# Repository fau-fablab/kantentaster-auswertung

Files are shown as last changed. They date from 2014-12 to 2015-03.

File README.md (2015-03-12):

kantentaster-auswertung
=======================

##motivation
Initially CNC mills do not "know" where the material is.
If you want to mill through the material, you have to know exactly where your material is relatively to the machine coordinate system.

For this the typical tool is a 3D probe.
However this probe cannot simply be connected to the controller of the mill.
This project is a Schmitt-triggered current loop to adapt the probe to the controller.

##circuit
The typical design for such a 3D probe (in our case a Renishaw) is that you have a contact which opens upon touching something with the tip of the probe.
When not touching anything the resistance of the probe is in the range of 20k.
When touching something the resistance becomes very large.

To have a robust measurement this circuit uses a current loop.
It consists of a constant-current-source which constantly puts a current of 1mA through the sensor.
Attached to this circuit is a Schmitt-trigger.
The hysteresis levels are configurable, because the trigger has to be fine tuned "in field".

Finally the output is separated from the controller with an optocoupler, because the sensor cable runs through a potentially rough environment.

----------------------
##version history
The first version of the PCB is in directory ```kantentaster_platine```. This version did not work. A complete redesign and current development version is in ```kantentaster_v2```.

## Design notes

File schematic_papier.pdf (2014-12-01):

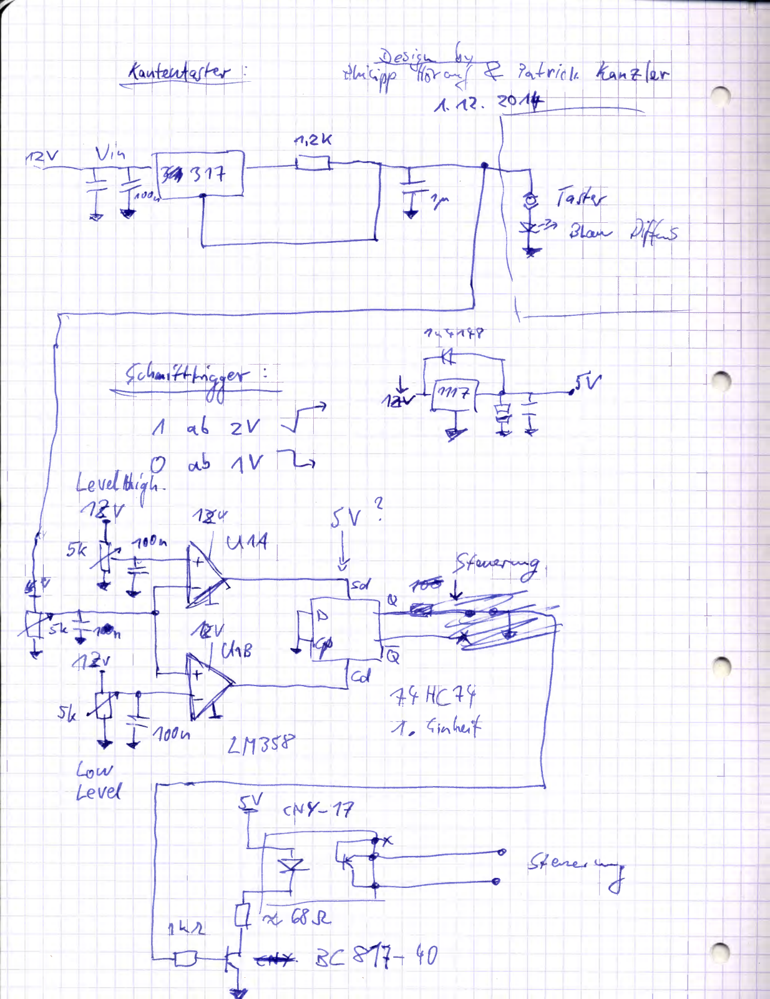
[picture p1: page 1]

-,1 ,.:c,~ T.,, -1-rirf, 4:.A„ ~ (o,.,..

A- '17. <~ L- --;-.

t

} 1
r

\/ cN Y- 11

.___--
~ '8JL
erO'- ?.C 1- Y 0

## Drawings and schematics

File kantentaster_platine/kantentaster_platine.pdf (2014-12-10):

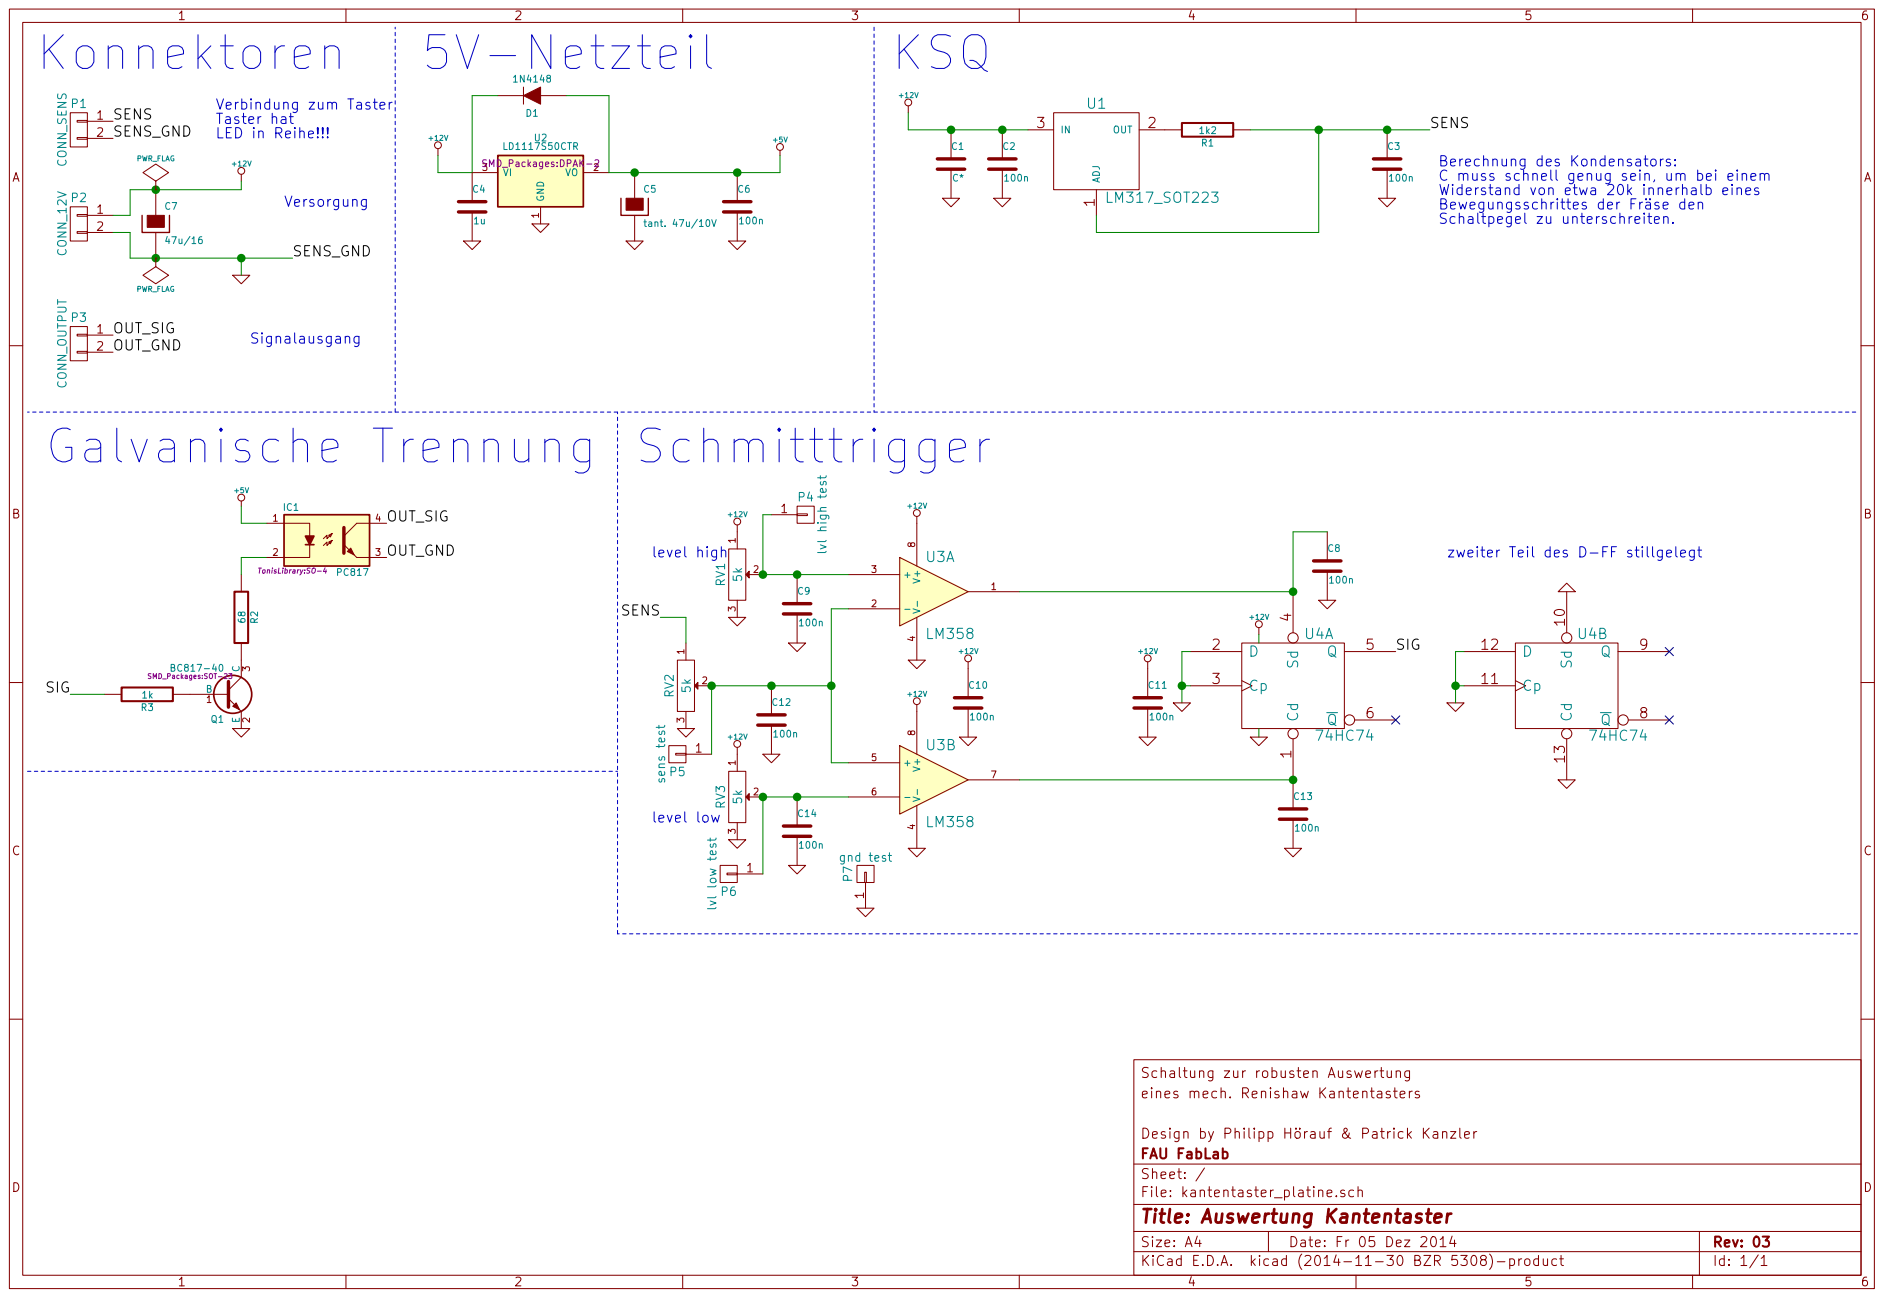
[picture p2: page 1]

Berechnung des Kondensators:
C muss schnell genug sein, um bei einem Widerstand von etwa 20k innerhalb eines Bewegungsschrittes der Fräse den

zweiter Teil des D-FF stillgelegt C4

File: kantentaster_platine.sch Sheet: / FAU FabLab Design by Philipp Hörauf & Patrick Kanzler eines mech. Renishaw Kantentasters Schaltung zur robusten Auswertung

Id: 1/1 Title: Auswertung Kantentaster

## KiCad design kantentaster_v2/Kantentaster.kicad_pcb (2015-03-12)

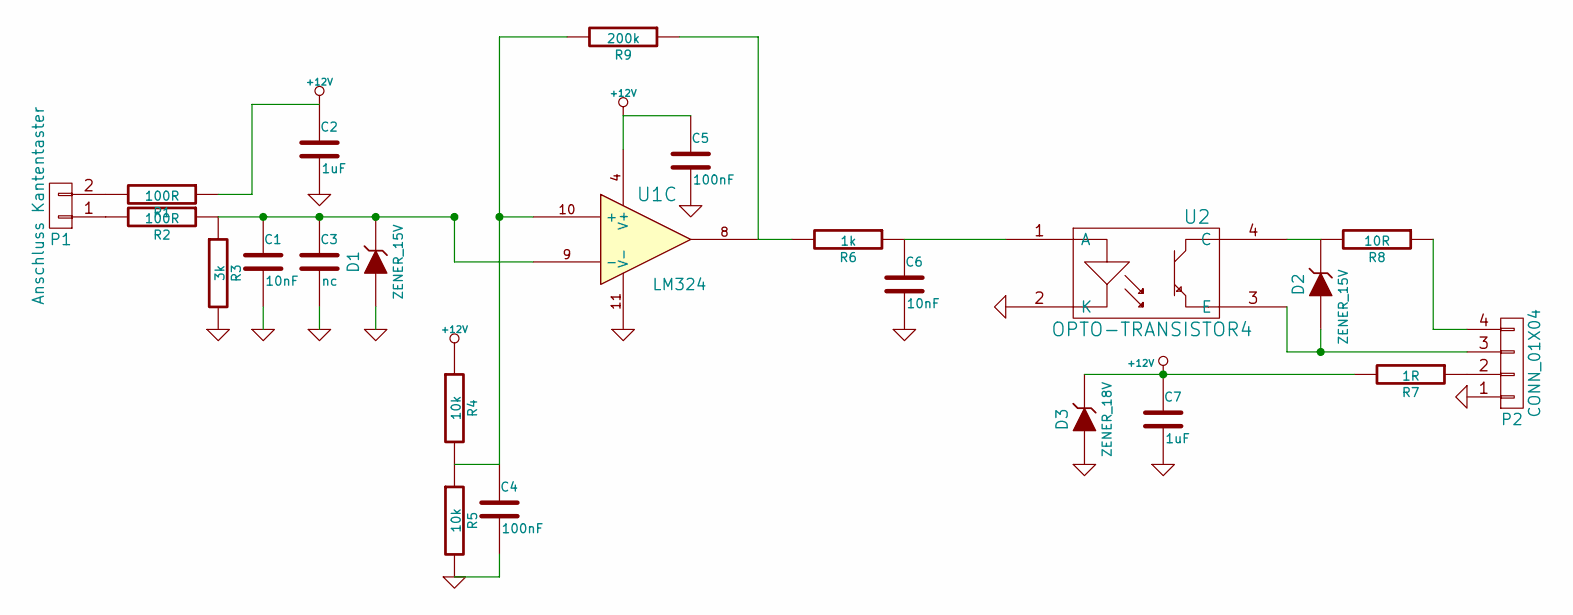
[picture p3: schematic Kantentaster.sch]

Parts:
C1, C6: 10nF; C_0603
C2: 1uF; C_1206
C3: nc; C_0805
C4, C5: 100nF; C_0603
C7: 1uF; C_0805
D1: ZENER_15V; Diode-SMB_Handsoldering
D2: ZENER_15V; Diode-SMA_Handsoldering
D3: ZENER_18V; Diode-SMB_Handsoldering
P1: Anschluss Kantentaster; Pin_Header_Angled_1x02
P2: CONN_01X04; Pin_Header_Angled_1x04
R1, R2: 100R; R_0805
R3: 3k; R_0805
R4, R5: 10k; R_0805
R6: 1k; R_0805
R7: 1R; R_0805
R8: 10R; R_0805
R9: 200k; R_0805
U1: LM324; SOIC-14_N
U2: OPTO-TRANSISTOR4; SO-4

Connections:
+12V: C2.1, C5.1, C7.1, D3.2 (K), R1.1, R4.1, R7.2, U1.4 (V+)
GND: C1.2, C2.2, C3.2, C4.2, C5.2, C6.2, C7.2, D1.1 (A), D3.1 (A), P2.1, R3.2, R5.2, U1.11 (V-), U2.2 (K)
unnamed: C1.1, C3.1, D1.2 (K), R2.1, R3.1, U1.9 (-)
unnamed: C4.1, R4.2, R5.1, R9.2, U1.10 (+)
unnamed: C6.1, R6.1, U2.1 (A)
unnamed: D2.1 (A), P2.3, U2.3 (E)
unnamed: D2.2 (K), R8.2, U2.4 (C)
unnamed: P1.1, R2.2
unnamed: P1.2, R1.2
unnamed: P2.2, R7.1
unnamed: P2.4, R8.1
unnamed: R6.2, R9.1, U1.8

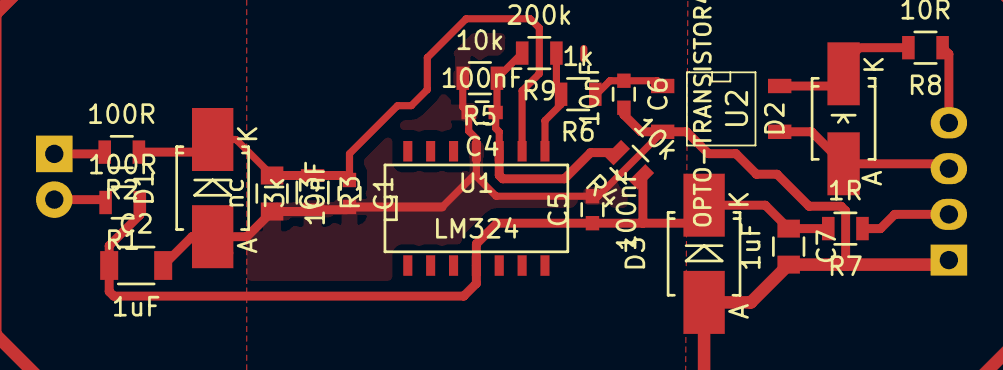
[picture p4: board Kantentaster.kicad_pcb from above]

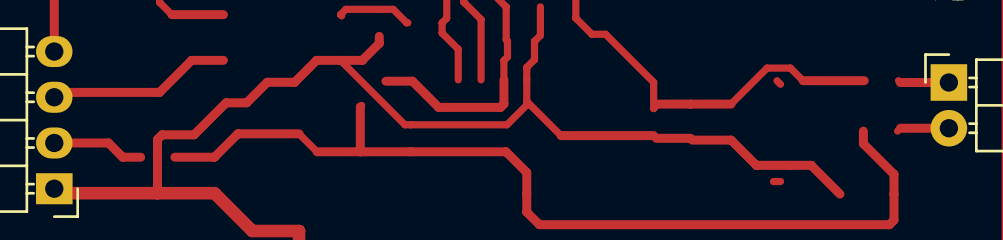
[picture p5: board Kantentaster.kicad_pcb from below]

Board: 2 copper layers, 23 parts (2 on the bottom side), 12 nets.

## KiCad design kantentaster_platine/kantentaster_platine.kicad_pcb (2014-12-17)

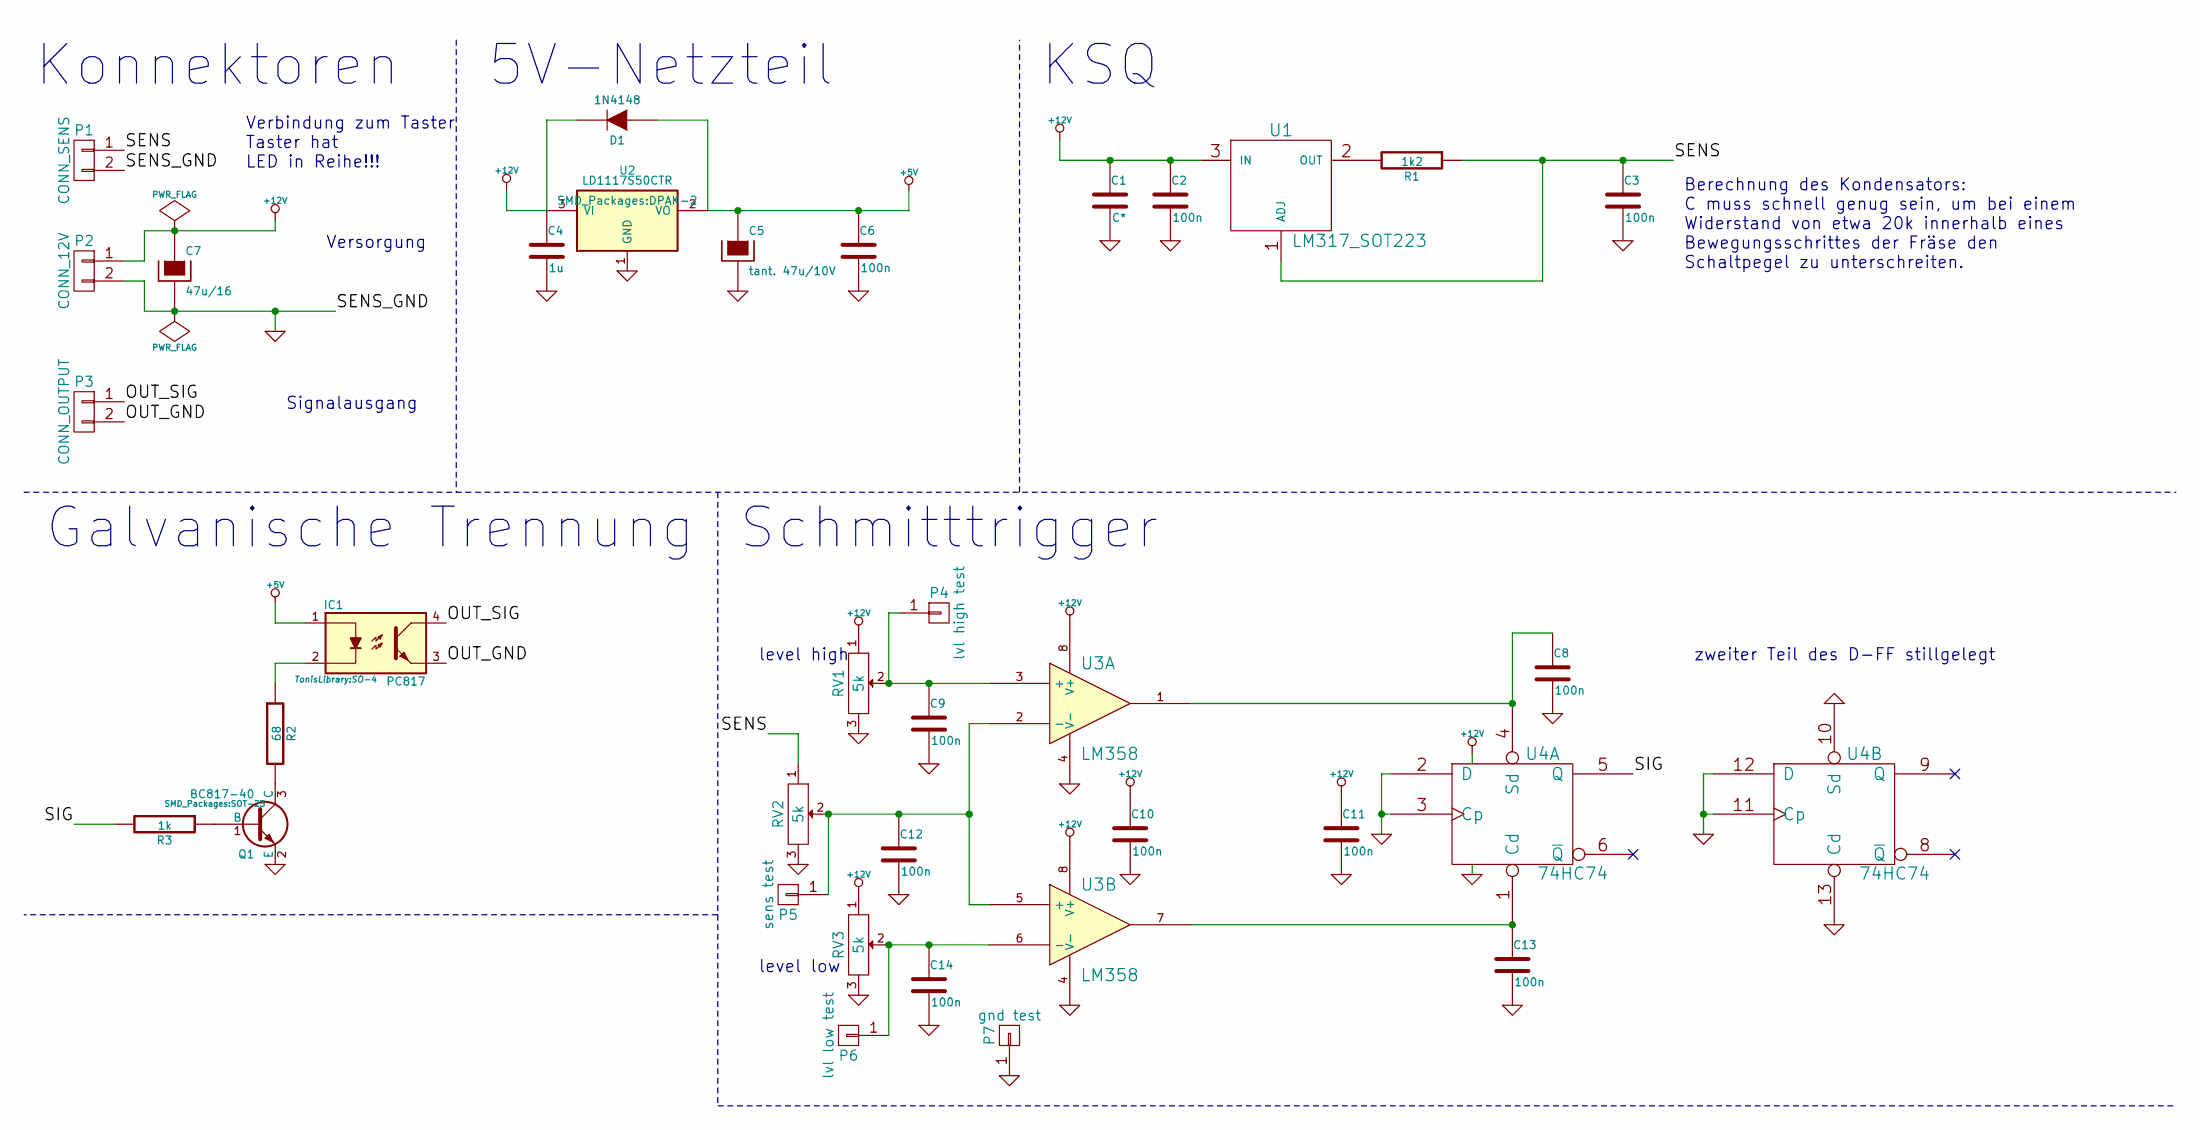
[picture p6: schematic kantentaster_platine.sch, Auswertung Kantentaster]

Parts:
C1: C*; C_0805
C2, C3, C6, C8, C9, C10, C11, C12, C13, C14: 100n; C_0805
C4: 1u; C_0805
C5: tant. 47u/10V; TantalC_SizeD_EIA-7343_Reflow
C7: 47u/16; c_elec_6.3x7.7
D1: 1N4148; Diode-MiniMELF_Standard
IC1: PC817; SO-4
P1: CONN_SENS; AK300-2
P2: CONN_12V; AK300-2
P3: CONN_OUTPUT; AK300-2
P4: lvl high test; Measurement_Point_Round-SMD-Pad_Big
P5: sens test; Measurement_Point_Round-SMD-Pad_Big
P6: lvl low test; Measurement_Point_Round-SMD-Pad_Big
P7: gnd test; Measurement_Point_Round-SMD-Pad_Big
Q1: BC817-40; SOT-23
R1: 1k2; SMD-0805
R2: 68; SMD-0805
R3: 1k; SMD-0805
RV1, RV2, RV3: 5k; Potentiometer_WirePads_Small
U1: LM317_SOT223; SOT-223
U2: LD1117S50CTR; DPAK-2
U3: LM358; DIP-8__300_ELL
U4: 74HC74; SOIC-14_W

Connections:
+5V: C5.1, C6.1, D1.1 (A), IC1.1, U2.2 (VO)
+12V: C1.1, C2.1, C4.1, C7.1, C10.1, C11.1, D1.2 (K), P2.1, RV1.1, RV3.1, U1.3 (IN), U2.3 (VI), U3.8 (V+), U4.14 (VCC)
/OUT_GND: IC1.3, P3.2
/OUT_SIG: IC1.4, P3.1
/SENS: C3.1, P1.1, R1.1, RV2.1, U1.1 (ADJ)
/SIG: R3.2, U4.5 (Q)
GND: C1.2, C2.2, C3.2, C4.2, C5.2, C6.2, C7.2, C8.2, C9.2, C10.2, C11.2, C12.2, C13.2, C14.2, P1.2, P2.2, P7.1, Q1.2 (E), RV1.3, RV2.3, RV3.3, U2.1 (GND), U3.4 (V-), U4.2 (D), U4.3 (Cp), U4.7 (GND), U4.10 (Sd), U4.11 (Cp), U4.12 (D), U4.13 (Cd)
unnamed: C8.1, U3.1, U4.4 (Sd)
unnamed: C9.1, P4.1, RV1.2, U3.3 (+)
unnamed: C12.1, P5.1, RV2.2, U3.2 (-), U3.5 (+)
unnamed: C13.1, U3.7, U4.1 (Cd)
unnamed: C14.1, P6.1, RV3.2, U3.6 (-)
unnamed: IC1.2, R2.1
unnamed: Q1.1 (B), R3.1
unnamed: Q1.3 (C), R2.2
unnamed: R1.2, U1.2 (OUT)

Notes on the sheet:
Konnektoren
5V-Netzteil
KSQ
Galvanische Trennung
Schmitttrigger
Verbindung zum Taster Taster hat LED in Reihe!!!
Versorgung
Signalausgang
level low
level high
zweiter Teil des D-FF stillgelegt
Berechnung des Kondensators: C muss schnell genug sein, um bei einem Widerstand von etwa 20k innerhalb eines Bewegungsschrittes der Fräse den Schaltpegel zu unterschreiten.

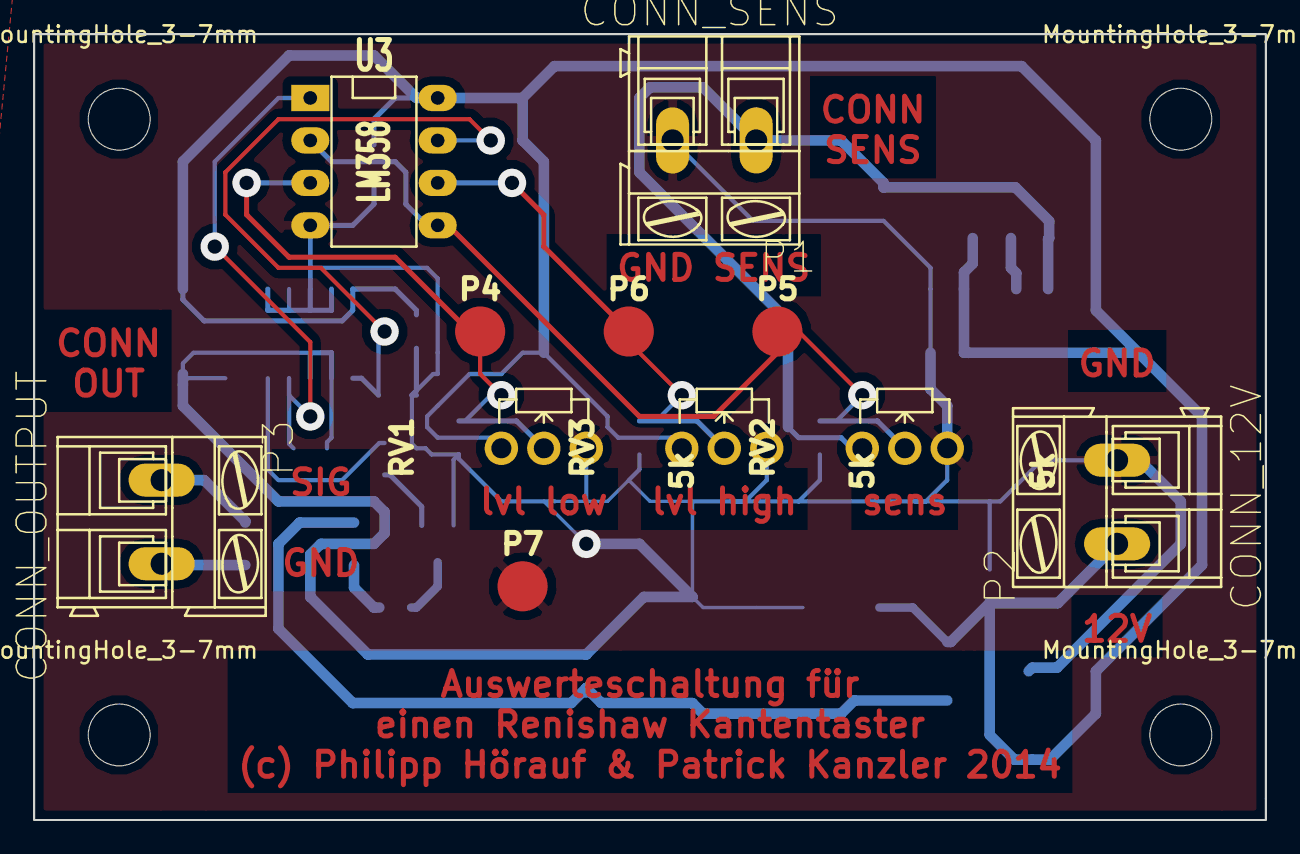
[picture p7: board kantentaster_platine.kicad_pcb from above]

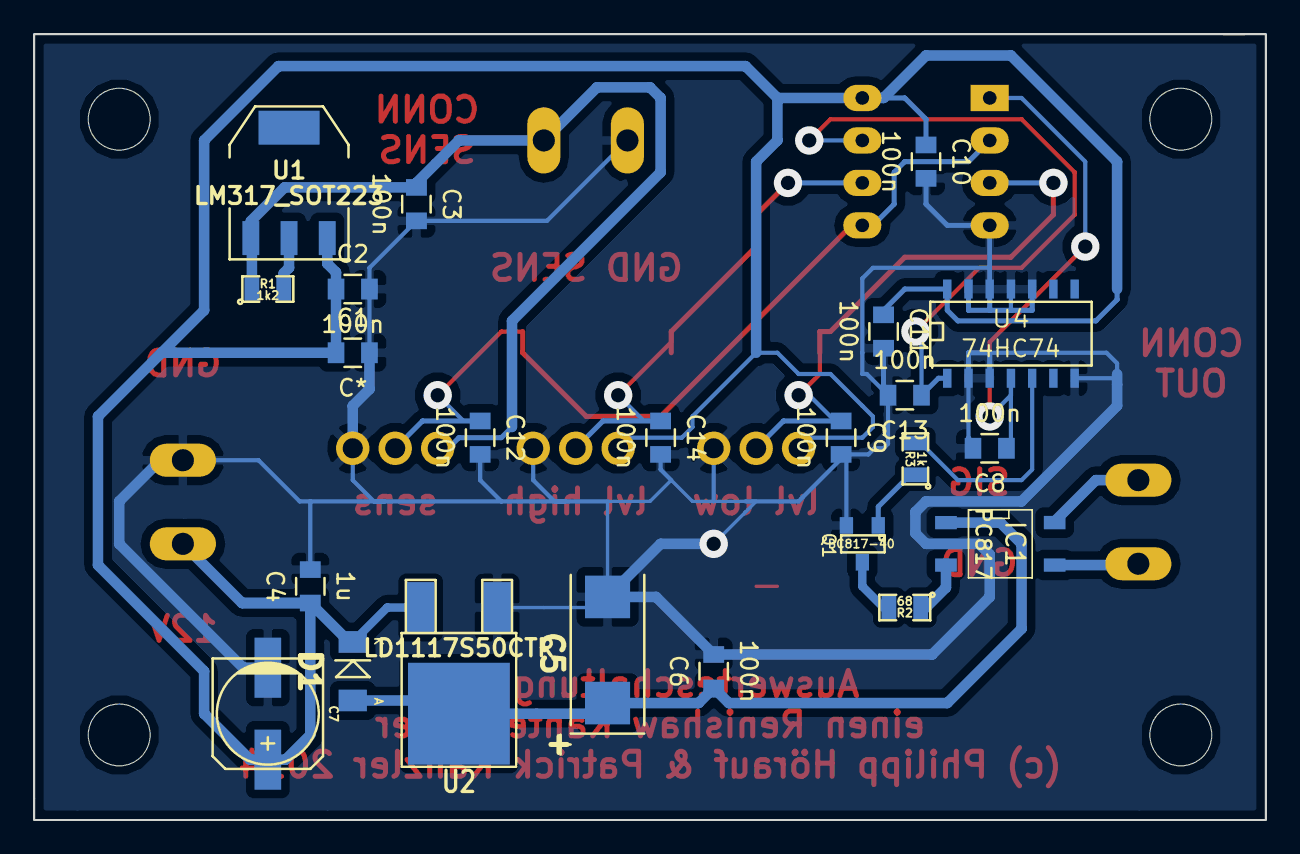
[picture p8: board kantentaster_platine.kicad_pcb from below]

Board: 2 copper layers, 73.7 x 47.0 mm, 38 parts (23 on the bottom side), 16 nets.

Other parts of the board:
MountingHole_3-7mm, MountingHole_3-7mm#2, MountingHole_3-7mm#3, MountingHole_3-7mm#4: VAL**; MountingHole_3-7mm

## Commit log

2014-12-01 Schaltplan für die Kantentaster-Auswertung
2014-12-10 Designfiles eingecheckt
    [kantentaster_platine.kicad_pcb, kantentaster_platine.sch]
2014-12-17 leiterbahn an messpad entfernt (optische Korrektur)
    [kantentaster_platine.kicad_pcb]
2015-02-14 Platine war Fail, TODO für nochmal machen ergänzt, wenn fertig mit neuen Bauteilen sauber aufbauen
    [kantentaster_platine.sch]
2015-02-24 Projekt erstellt, Schaltplan fertig
    [Kantentaster.kicad_pcb, Kantentaster.sch]
2015-02-28 anpassungen am schaltplan und layout
    [Kantentaster.kicad_pcb, Kantentaster.sch]
2015-03-01 Mitkopplung hinzugefügt
    [Kantentaster.kicad_pcb, Kantentaster.sch]
2015-03-05 finale Version
    [Kantentaster.kicad_pcb, Kantentaster.sch]
2015-03-05 Fehler des ersten Prototypen behoben
    [Kantentaster.kicad_pcb, Kantentaster.sch]
2015-03-12 move layout by @ep092 into subfolder as preparation of merge
    [Kantentaster.kicad_pcb, Kantentaster.sch]
